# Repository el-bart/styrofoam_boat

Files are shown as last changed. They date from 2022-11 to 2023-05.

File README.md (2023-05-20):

# styrofoam boat

toy boat project, made out of styrofoam sheets and 3D-printed parts.
some random electronics added on top, to control it from the computer remotely.

note - it's mostly a junk-bin build.
you'll most likely not want to reproduce it 1:1, but adjust to what you have, instead.

## LoRa modules

in the design `E32-433T20D` LoRa modules are used.
it's powered with 5V, but logic operates at 3.3V and is NOT 5V tolerant.

SW assumes modules are operating in 115200 bps 8N1 mode.
this is not the default mode, though.
in order to program these, `M0` and `M1` ports must be pulled high (3.3V).
then special, binary sequence must be sent, namely:

> C000003C2E00

it's represented in hex.
value must be sent in binary, using 9600bps 8N1 mode.
this will write the value and persist it.
from now on each module will send data wirelessly using 19200bps 8N1.
user-facing interface will accept data to be sent using 115200bps 8N1.
both modules shall be programmed the same way.

the easiest way to interface with these are prototyping boards and USB-to-serial interfaces.
note that the interface must operate at 3.3V.

if other operational parameters are needed, command for programming different work modes must be constructed.
to help with this see source code under: `common/LoRa/Ebyte`.
it allows to specify required settings and after compiling prints out given settings.

## final thoughts / lessons learned

### good

* LoRa modules worked like a charm (despite "guaranteed" latency)
* sealing worked flawlessly
* safety feature to stop engine and 0-out rudder in case of connectivity issues saved the boat countless times

### bad and ugly

* rudder blade was too shallow. making it go deeper would provide more authority over the boat
* screw was not deep enough - it should be fully submerged, couple cm under water
* rudder must be perfectly centered behind the screw - 3mm off is enough to make a bit difference wrt turning direction agility
* old, junk-bin analog cameras are really not worth the effort... :P
* screw should be as close to 0 deg angle wrt waterline as possible - otherwise it's just an energy loss
* make sure engine has enough power to drive the boat against the wind
* ship's side shall not be too high, as it then acts as a sale, even on a small wind

### misc notes

* have a small pontoon at hand - just in case (had couple of close calls)
* tall, rubber boots are helpful at the pond
* make sure to check transcievers range before learning it the hard way at the pond ;)

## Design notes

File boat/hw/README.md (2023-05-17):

# wiring

arduino is connected to E32-433T20D LoRa module via level-shifter.
this is needed since arduino is operating at 5V, while LoRa module at 3.3V and is not 5V-tolerant.

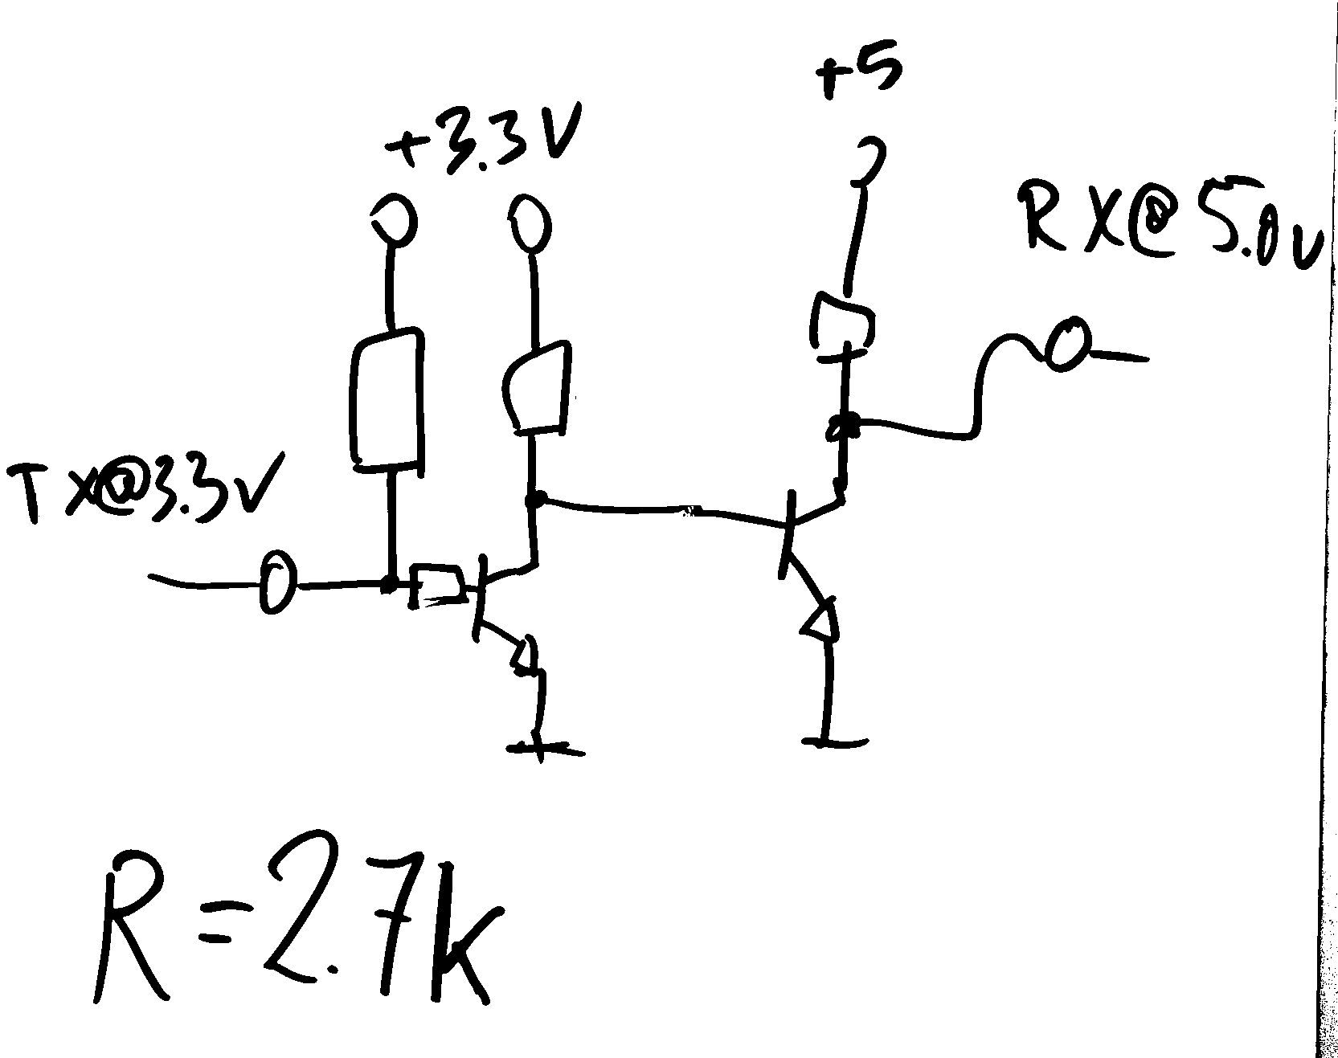
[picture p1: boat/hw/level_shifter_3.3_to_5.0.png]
level shifter


additionally, LoRa module's `M0` and `M1` pins must be pulled low, in order for it to operate.

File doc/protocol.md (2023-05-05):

# control protocol

communication is unidirectional (from computer to boat).
each package consists of 3 bytes:
1. `servo_pos` (0-127 that's mapped to +-60 deg)
2. `engine_speed` (0-64, that's mapped to 0-100% PWM)  + `engine_dir` (1 bit: 1==F, 0=B)
3. `checksum` (XOR of previous 2 bytes)

## stream (re)synchronization
bytes 1 and 2 always have MSb == 0.
byte 3 always has MSB == 1.

## servo position
servo position is encoded in 7, lower bits of a byte.

## engine speed
engine speed is encoded using 6, lower bits of a byte.
7th bit is a direction bit:
* 0 == backward
* 1 == forward

## encoding
data sent (and received) as a 3.3V UART, configured for 115200 bps.

radio link is established using LoRa module E32-433T20D.
default setings of the module are used, i.e.:
- 115200 bps serial speed
- 19200 bps wireless speed

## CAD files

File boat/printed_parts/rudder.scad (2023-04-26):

use <m3d/fn.scad>

eps = 0.01;

module rudder_hold()
{
  module slot(slot_h, dh=0)
  {
    h = slot_h + dh;
    // top-down and center
    hull()
    {
      d = 6;
      for(dy=[-1,+1])
        translate([0, dy*(36/2-d/2), 0])
          cylinder(d=d, h=h, $fn=fn(50));
      cylinder(d=8+2, h=h);
    }
    // left-right
    hull()
    {
      d = 5;
      for(dx=[-1,+1])
        translate([dx*(20/2-d/2), 0, 0])
          cylinder(d=d, h=h, $fn=fn(50));
    }
  }

  core_size = [25, 40, 4];
  slot_h = 1.5 + 0.5;
  difference()
  {
    translate(-0.5*[core_size[0], core_size[1], 0])
      cube(core_size);
    translate([0, 0, core_size[2]-slot_h])
      slot(slot_h=slot_h, dh=eps);
  }
}

module rudder_body()
{
  h = 137;
  translate([0, 0, -h])
    resize([5, 40, h])
      cylinder(d=5, h=h, $fn=fn(100));
}


module rudder()
{
  rotate([0, 180, 0])
  {
    rudder_hold();
    rudder_body();
  }
}


rudder();

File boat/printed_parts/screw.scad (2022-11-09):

eps = 0.01;
angle = 30;
blades = 5;
d = 15;
h = 2;
l = 30;

module blade()
{
  dx = l-d/2;
  off = d*cos(angle) - h*cos(90-angle);
  translate([0, -off/2, 0])
    rotate([angle, 0, 0])
      {
        translate([dx, d/2, 0])
          cylinder(d=d, h=h, $fn=60);
        cube([dx, d, h]);
      }
}


module screw()
{
  module base()
  {
    difference()
    {
      union()
      {
        // core
        cylinder(d=d, h=d, $fn=60);
        // blades
        for(r=[0:blades-1])
          rotate([0, 0, r*360/blades])
            blade();
      }
      // rod hole
      translate([0, 0, -eps])
        cylinder(d=3.5, h=d+2*eps, $fn=60);
    }
  }
  intersection()
  {
    q = d*sin(angle);
    dh = h*sin(90-angle);
    base();
    translate([0, 0, dh])
      cylinder(d=3*l, h=q-dh);
  }
}

screw();

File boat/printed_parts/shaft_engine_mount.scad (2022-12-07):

use <m3d/fn.scad>

module shaft_engine_mount(d_mnt_eng=9,   h_mnt_eng=5,
                          d_mnt_shaft=3, h_mnt_shaft=10,
                          wall=2, spacing=0.75)
{
  eps = 0.01;
  h = h_mnt_eng + h_mnt_shaft + wall;
  d_ext = d_mnt_eng+spacing+2*wall;
  difference()
  {
    cylinder(d=d_ext, h=h, $fn=fn(50));
    // engine mount in the top
    translate([0,0,h-h_mnt_eng])
      cylinder(d=d_mnt_eng+spacing, h=h_mnt_eng+eps, $fn=fn(100));
    // shaft mount in the bottom
    translate([0,0,-eps])
      cylinder(d=d_mnt_shaft+spacing, h=h_mnt_shaft+eps, $fn=fn(50));
    // M2 screw hole for holding shaft in place
    {
      d_screw = 2+0.25;
      h_screw = 2*d_ext;
      translate([0, h_screw/2, max(h_mnt_shaft-2*d_screw, d_mnt_shaft/2)])
        rotate([90, 0, 0])
          cylinder(d=d_screw, h=h_screw, $fn=fn(50));
    }
  }
}


shaft_engine_mount();

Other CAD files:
boat/printed_parts/shaft_oring_holder.scad
boat/printed_parts/m3d/fn.scad
boat/printed_parts/m3d/inner_shell.scad
boat/printed_parts/m3d/outer_shell.scad
boat/printed_parts/m3d/rounded_cube.scad
boat/printed_parts/m3d/screw_head_hex.scad

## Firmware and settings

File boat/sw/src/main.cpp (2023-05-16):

#include <Arduino.h>
#include <Servo.h>
#include <avr/wdt.h>
#include "ProtoFsm.hpp"

Servo servo;
auto constexpr pin_servo = 2;
auto constexpr pin_engine_enable = 5;   // L298: enable pin  -> pin 6
auto constexpr pin_engine_input_a = 11; // L298: input pin C -> pin 5
auto constexpr pin_engine_input_b = 12; // L298: input pin D -> pin 7
auto constexpr use_debug_writes = false;
ProtoFsm fsm;

namespace
{
template<typename T>
void debug_write(T const& t)
{
  if(use_debug_writes)
    Serial.write(t);
}

void apply_engine(Frame const& frame)
{
  if( frame.engine_speed() == 0u )
  {
    digitalWrite(pin_engine_enable, 0);
    return;
  }
  analogWrite( pin_engine_enable, frame.engine_speed() );
  switch( frame.engine_direction() )
  {
    case EngineDir::Forward:
          digitalWrite(pin_engine_input_a, 1);
          digitalWrite(pin_engine_input_b, 0);
          break;
    case EngineDir::Reverse:
          digitalWrite(pin_engine_input_a, 0);
          digitalWrite(pin_engine_input_b, 1);
          break;
  }
}

void apply_servo(Frame const& frame)
{
  servo.write( frame.rudder_angle() );
}

bool apply_outputs(uint8_t byte)
{
  if( not fsm.add_byte(byte) )
    return false;
  auto const frame = fsm.pop();
  apply_engine(frame);
  apply_servo(frame);
  return true;
}

void start_position()
{
  auto constexpr start_servo = 127/2;
  auto constexpr start_engine = 0;
  apply_outputs(start_servo);
  apply_outputs(start_engine);
  apply_outputs((start_servo ^ start_engine) | 0x80);
}
}

void setup()
{
  Serial.begin(115200);     // RX == 0, TX == 1
  servo.attach(pin_servo);
  {
    pinMode(pin_engine_enable, OUTPUT);
    pinMode(pin_engine_input_a, OUTPUT);
    pinMode(pin_engine_input_b, OUTPUT);
  }
  start_position();
  {
    wdt_disable();
    wdt_enable(WDTO_1S);
  }
  debug_write("booted\n");
}


namespace
{
struct SerialByte
{
  SerialByte() = default;
  explicit SerialByte(uint8_t byte):
    is_set_{true},
    byte_{byte}
  { }

  bool is_set_{false};
  uint8_t byte_{0};
};

SerialByte read_serial()
{
  while(Serial.available() < 1)
  { }
  auto byte = Serial.read();
  if(byte < 0)
    return {};
  debug_write('.');
  return SerialByte{ static_cast<uint8_t>(byte) };
}
}

void loop()
{
  auto const serial_byte = read_serial();
  if(not serial_byte.is_set_)
    return;
  if( apply_outputs(serial_byte.byte_) )
    debug_write('#');
  wdt_reset();
}

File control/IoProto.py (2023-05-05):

from enum import Enum
import serial
import time

class Boat:
    def __init__(self, port):
        self._sp = serial.Serial(port, 115200)
        self._next_frame_after = 0.0

    # eng_speed = -100..+100 [%] (0 == stop)
    # servo_pos = -60..+60 [deg] (0 == center)
    def send(self, eng_speed, servo_pos, output=False):
        # avoid buffering - always send latest instead
        if self._sp.out_waiting > 0:
            return False
        # give time for LoRa module to send
        if time.time() < self._next_frame_after:
            return False
        # actual sending
        frame = bytearray()
        frame.append( self._encode_servo_pos(servo_pos) )
        frame.append( self._encode_speed(eng_speed) )
        frame.append( self._encode_checksum(frame) )
        self._sp.write(frame)
        if output:
            print("{:02x} {:02x} {:02x}".format(frame[0], frame[1], frame[2]))
        # must wait >20ms after each transmission, to make sure LoRa module sends out the data
        self._sp.flush()
        self._next_frame_after = time.time() + 0.025
        return True

    def _encode_speed(self, s):
        assert( -100 <= s and s <= +100 )
        dir_bit = 0x00 if s < 0 else 0x40
        s = abs(s)
        s = int(s/100 * 63)
        assert( 0 <= s and s <= 63 )
        return dir_bit | s

    def _encode_servo_pos(self, p):
        assert( -60 <= p and p <= +60 )
        p = -p
        p = p + 60
        p = int(p/(2*60) * 127)
        assert( 0 <= p and p <= 127 )
        return p

    def _encode_checksum(self, frame):
        x = frame[0] ^ frame[1]
        return x | 0x80

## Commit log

2022-11-09 build for 3D printed elements
    [fn.scad, inner_shell.scad, outer_shell.scad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]
2022-11-09 screw prototype
    [screw.scad]
2022-11-09 smaller angle, bug bigger blades
    [screw.scad]
2022-11-09 removed dead code
    [screw.scad]
2022-12-07 oring holder for shaft added
    [shaft_oring_holder.scad]
2022-12-07 oring holder polished to the point of being useful :P
    [shaft_oring_holder.scad]
2022-12-07 engine-to-shaft mount element
    [shaft_engine_mount.scad]
2022-12-07 fixed model's height
    [shaft_engine_mount.scad]
2023-04-13 printed parts moved to the 'boat' section
    [fn.scad, inner_shell.scad, outer_shell.scad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]
2023-04-13 build for arduino nano with Servo library
2023-04-13 test app for sweeping servo back and forth
2023-04-13 added main engine PWM, too
2023-04-16 added helper class for encoding data into serial frames + a test servo sweep application
2023-04-16 draft of Frame and ProtoFsm for processing input data
2023-04-16 decoding positions and pseeds from a frame moved to Frame.hpp
2023-04-16 fixed order of steps (servo then engine)
    [IoProto.py]
2023-04-16 fixed checking of frame is correct
2023-04-16 helper class for handling joystick input device
2023-04-16 added pretty-printing of read values
2023-04-26 serial speed changed to 1200bps, to accomodate to shitty wireless link
2023-04-26 added queuing send, before printing data out on the screen
2023-04-26 removed redundant engine pin
2023-04-26 engine enable is back to pin 5
2023-04-26 added mapping from raw throttle values to 75-100 range, that is actually 'runnable' on the engine
2023-04-26 placeholder for rudder model
    [rudder.scad]
2023-04-26 printing for strength by default
2023-04-26 rudder model completed
    [rudder.scad]
2023-04-26 no ironing + faster rudder print (with cooling)
2023-04-29 rudder direction is inverted
    [IoProto.py]
2023-04-29 helper script for starting camera preview
2023-04-29 camera preview is now executable
2023-05-03 1200 bps -> 9600 bps, as will be the case for LoRa modules
2023-05-03 added 25ms pause between actual sending of frames
2023-05-03 fixed a default wireless speed
2023-05-03 add moved rotating values to a place of usage of encoders
2023-05-03 helper program for printing out modem settings
2023-05-03 added printing codes for default and faster modes
2023-05-05 fixed 2 syntax errors
    [IoProto.py]
2023-05-05 serial and wireless speeds changed
